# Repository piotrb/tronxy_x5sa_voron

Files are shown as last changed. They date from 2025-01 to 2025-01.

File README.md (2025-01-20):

# TronXY X5SA -> Voron Trident Conversion

Work in Progress

I opted for "topic" based mini readmes, so have a look in each folder and see what's there.

This should be mostly complete, ther's better ways to organize this all I'm sure, but this may get you somewhere closer to a full trident conversion.

Given this is fairly ... not step by step :) .. if you want to reach out to me I'm happy to help. 

You can find me as `.noobbait` on discord.

## Old Outdated Docs / V1 Conversion / etc

Ther's stuff in the [Archive](Archive) folder which is older .. especially the Old Docs folder there may have a bunch of additional detail that's not in these folders here.

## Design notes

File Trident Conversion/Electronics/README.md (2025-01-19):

This was a personal choice, but I really wanted the Inverted Electronics Bay option, and I also was a big fan of the EMS system.

So There is a few slight mods here for this particular purpose.

I also highly recommend swapping our the stock power supply for a genuine Meanwell PSU.

A Meanwell 350W PSU is thinner, so better airflow, and generally should just be safer :) .. Also, it only runs its Fan when it needs, to, rather than constanly .. 

I otherwise replaces all the other electronics, so you will need to make your own choices here.

You will also need to buy a proper power receptacle, the Tronxy one is odd sized and doesn't fit the "Adamtech" style, it felt a lot easier to just buy that rather than trying to make it fit.

BOM:

Item | qty | Notes
--- | --- | ---
Meanwell 350W PSU | 1 |
Power Recepticle | 1 |

## Chains

I tried to use the stock chains .. they're very crude .. 

I ended up just ordering some better ones from Aliexpress .. so the standard voron chain mounts work nicely.

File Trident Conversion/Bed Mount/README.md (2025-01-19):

Bed mounting was one of the more challenging parts of this conversion .. 

And a big reason why I gave up on the V1 conversion .. 

The "proper" voron bed setup is one of the most expensive parts of the printer, so I really wanted to be able to to avoid having to make that a requirement.

I ended up re-using some of the hardware that came with the bed .. those 10x10 square rods work really well to mount the very specific 6 screw mount .. 

Those 10x10 rods had to be cut down to size,

This is what this all looks like assembled:
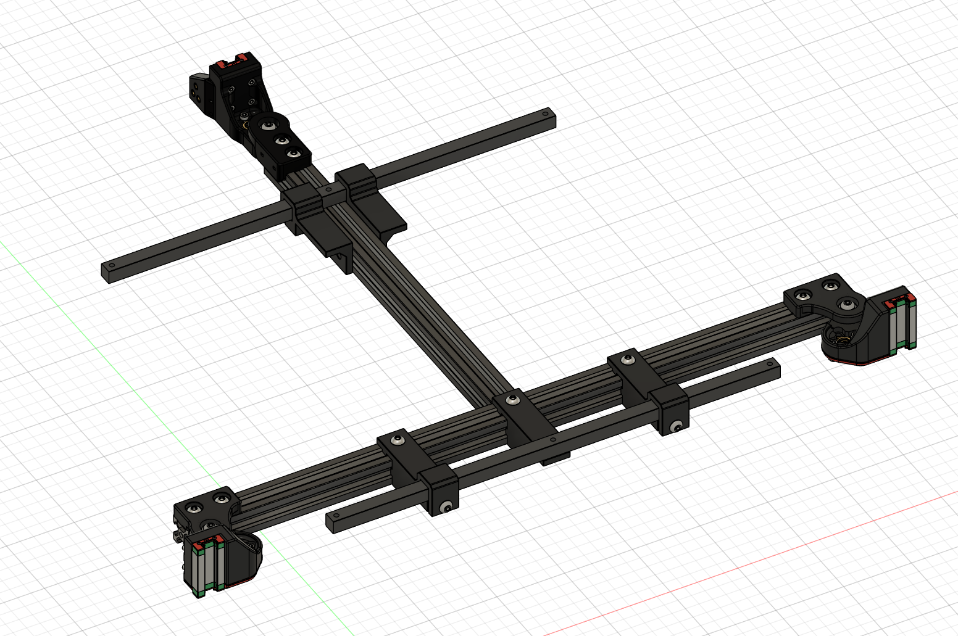
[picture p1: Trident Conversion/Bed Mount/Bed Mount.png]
Bed Mount


The pieces which fit around the 10x10 use a M5 25mm bolt, with a hex nut to secure it to the 10x10 rods.
With standard M5x10 bolts going into T-nuts or insert nuts to attach them to the extrusions.

I did away with the adjustment "wheels" and just used M3 nylock nuts to secure the bed screws.

I also swapped out the springs for these silicons spacers: https://www.aliexpress.com/item/1005003344878167.html
(it feels like it helped make things smoother)

Securing the back center bed screw is a bit finicky since it aligns with the 2020 extrusion.

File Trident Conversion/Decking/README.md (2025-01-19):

Nothing special here other than needing specifically sized decking.

BOM:

Item | Dimensions | Qty | Note
-|-|-|-
Corrugated Plastic | 473mm x 503mm | 1 | Back Panel
Corrugated Plastic | 458mm x 488mm | 1 | Decking
Corrugated Plastic | 478mm x 508mm | 1 | Bottom (optional)

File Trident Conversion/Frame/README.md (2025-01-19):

Ah frame .. 

You will need to buy some things here .. 

BOM:

Item | qty | Notes
--- | --- | ---
2020 Extrusion 420mm | 2 | (X axis) M5 tap on both ends
2020 Extrusion 360mm | 1 | (back horizontal) no tap
2020 Extrusion 405mm | 1 | (back vertical) M5 tap on one side only (both sides is ok, but only need one)

I had good success with this store: https://www.aliexpress.com/store/911747370 they have preset sized extrusions, but they will cut/tap them on request. They did that quite quickly for me and the packaging was great too, good padding, so there little change of damage in transit.

You can re-use the X extrusion from the Tronxy, but you will have to cut it down to size. It needs to be 450mm long.

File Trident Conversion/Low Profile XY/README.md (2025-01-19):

This is a special mod I made that fits around the 2040 extrusions the Tronxy uses.

The core pieces are the A/B Upper/Lower pieces.

This is a slightly less sturdy mount, but it doesn't waste any print volume.

I also gave the front idlers a similar treatment, but I did add some additional M3 holes so they can attach from a differnt direction, giving it all a pretty sturdy feel.

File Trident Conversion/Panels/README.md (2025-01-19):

## Panels:

You will want to get some 3mm acrylic panels

Exact dimensions coming .. 

Acrylic Transparent Panel 472mm x 502mm x 3mm | 1 | Top
Acrylic Transparent Panel 472mm x 544mm x 3mm | 2 | Sides
Acrylic Transparent Panel 472mm x 251mm x 3mm | 2 | Doors

Keep in mind that you likely will need to trim the panels for a final fit, so you will need a food file, or a dremel for this.

## Panel Clips

I wanted an easy way to remove my panels if needed .. I went through a few options here .. 

I ended up settling on these:

I had a bunch of spare M2 screws, so this seemed like a good option.
https://www.printables.com/model/643837-wide-voron-panel-snap-latch-with-lip-using-m2-scre

Ther's a M3 based option here, I didn't try it.
https://www.printables.com/model/702768-kit-for-removable-panelsdoors-for-voron-v2trident-

## Hinges:

I tried the clamping 270 degree hinges .. they kept slipping from the door .. so I switched to these:

https://github.com/VoronDesign/VoronUsers/tree/main/printer_mods/chrisrgonzales/270_degree_hinge

I also ended up needing to modify the way latches to work nicely .. see subfolders ..

I also use the latches from this, but I modified the "frame" side of the latch for a better fit/spacing. So feel free to use that or my mod, its not really specific to this conversion.

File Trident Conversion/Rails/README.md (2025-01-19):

Ther's a bunch of these .. and I definitely bought the wrong ones a few times :) 

BOM:

Item | qty | Notes
--- | --- | ---
350mm MGN9H | 2 | (for the Y)
450mm MGN12H | 1 | (for the X) -- this is wrong .. we need it to be 400mm I think

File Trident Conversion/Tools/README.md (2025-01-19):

## 105mm Y alignment spacer (print 2 of them)

this is used to align the Y axis when you're fastening the frame together.

Now I don't know if this was the best choice for sizing .. I feels a bit squisky in there .. 

I'm no longer sure why I opted for 105mm .. the Trident standard is actually 110mm .. so I don't necessarily recommend you follow my choice here ..

If I was doing this again I'd just do the voron standard here.

## the 115mm Extrusion Drill Guide

This is used to drill the access holes for attaching the Y axis crossbars

Many notes same as above .. it'd be 120mm per voron spec instead .. 

## Back Center Drill Guides

Print A and B (these should be printable diagonally on a 250mm print bed)

These just give you a nice way to drill the center access hole for the Back Z extrusion mount.

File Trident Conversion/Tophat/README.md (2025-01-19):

My particular choices necessitated a tophat .. (basically opting for umbilical .. which was always what I was going to do .. )

Needing custom sizing, and not really wanting to burn through rolls of ASA in prototyping this I decided for a very light weight tophat option.

I published this as a standalone mod:

https://www.printables.com/model/874142-minimal-tophat-using-4mm-coroplast-sides-flexible

If you need a tophat, you can give this a try. You can use the leftover coroplast from the decking/back/etc to use as side fillers.

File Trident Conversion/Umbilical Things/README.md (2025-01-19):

This folder is a bit of a catch all for a few odd mods I did to make everything work.

I ended up using this particular adapter for the back connector:

https://www.printables.com/model/326623-voron-trident-wire-cover-w-pg7-cable-gland-adapter

And the microswitch mount from here:

https://github.com/VoronDesign/VoronUsers/tree/main/printer_mods/Minsekt/Rear_Umbilical

This all worked out pretty well ...

I like these two because they together allow not needing a customized version of the AB motor mount system.

--

I don't have a lot of advice for the toolhead side of the umbilical .. 

I personally use the XOL toohead .. so the mounting is quite different, and I have my own mods here for that :) 

But there is plenty of PG7 cable gland adapters out there.

Just don't make the mistake I did and get the correct sized glands :)

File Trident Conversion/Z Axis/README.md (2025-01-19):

# Z Axis

## Z Mount Adapter

This piece allows you to use the stock Front Z motor mounts.

The Smaller version is for use with the inverted electronics mod mount variants.
The Regular is for the BOM variant.

You will need two of these, as well as:

* 4x M5x10 Socket Head Cap Screws
* 4x M5 Hex Nuts

## Z Motors .. 

I could have gone for the BOM lead screw motors .. but those tend to be expensive .. 

I did end up buying a set of "nicer" StepperOnline motors 

Also to have a matching set of motors to avoid any weirdness with having mismatched motors .. 

But you can totally do with the stock 2 Z motors, and then just add another ... similar one .. it *should* work, but YMMV :) 

The two Z screws that came with the Tronxy are the right length, you need another one of similar length for a full set for a trident.

I ended up going through a few options around the coupling of the motors and the lead screws .. in the end I ended up with these flexible couplings from Amazon that worked the best.

I would also recommend really carefully setting up your Z screw coupling, I had issues with the screw being a bit offset and rubbing on the leadscrew nut.

Speaking of which, I opted to get the POM leadscrew nuts, this worked out well for me, they seem to work well and are quiet.

Also, you know how the voron guide talks about keeping the leadscrew nut a but lose .. well you need that :) 

I also realized with some trial and error that you want to kind of offset the orientation of the screws that hold the nut .. 

- only 2 screws hold it, this is on purpose, this allows it some wiggle in the direction they're mounted.
- so assuming we use clock hand positions for the locations, you may want to set the back to 12 and 6, and the front (both of the front ones) to 3 and 9 .. this way the back can wiggle a bit forward and back, and the sides can wiggle a bit side to side. This should allow things to settle to a good position.

## Linear Rails

You will need 3x ~380mm linear rails (follow voron spec for the type and all, its just the length that changes)

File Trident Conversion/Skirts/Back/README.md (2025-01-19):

The back left and right pieces were fairly complex, they had the mounting for power/lan/usb/etc .. 

Also, it was the middle piece the stock build has of different sizes, so I just resized the center, use the side pieces from the stock build.

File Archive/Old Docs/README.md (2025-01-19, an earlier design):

This is a repo to track work I'm doing on converting a Tronxy x5sa to a Voron Chimera of some sort .. 

# High Level Objectives:

* Try to re-use as many parts as possible
* Try to make this into a gradual upgrade with "usable" milestones along the way.

# Milestones:

## 1. Open Frame V1.8 Style conversion

Goals:
* Mechanically everything works
* Printer *could* be enclosed at this point
* Some aspects could be rough and not quite pretty enough to request a serial
* At this phase, at least for me, I'll put on an Afterburner toolhead.
 * I have a few reasons:
   1. I have one leftover from my Switchwire when I upgraded it.
   2. I have some High Flow CHT heaters I've been itching to use, its easier to get volcano style mods for the AB .. they exist for the SB, but require an alternate whole Front piece .. which means I'd need to have two of those ready to go to be able to alternate between long and short nozzles ... 
   3. It just feels like a more modular design to hack on .. I've also been meaning to play with multi-material printing .. I even have a bunch of 2 in 2 out (and 2 in 1 out) heatsinks and whatnot .. my Switchwire was just annoying to try to build that onto :)
* Extra Credit: I've not seen a mod for this .. I'm going to try to see how I can either use the CW2 with the AB, or mod the CW1 so it mounts as easily as the CW2 (no back screws)

## 2. Enclosed V1.8 Style printer

Goals:
* Extra cost here, I will get Acrylic panels cut at this point
* I do plan to keep using coroplast for the opaque panels, its cheap and then I don't have to worry about the differences between the 1.8 and Trident Decking.
* This would qualify for a V1.8 Voron Serial
* Any final touches to make the electronics bay pretty and nicely cable routed.

## 3. Trident and beyond

* Start thinking about what would be needed to take this towards a trident design.
* I know the bed assembly will be a bit of a problem, so that will need some serious thought
* The rest actually shouldn't be too much of a problem, re-print a bunch of the parts, move the linear rails below the extrusions .. etc .. I'm already trying to hybridize Trident elements in the original design to make this as waste-less as possible.
* I'll likely wait until this phase to install the TAP, I have a kit for it kicking around, so I'm keen to know if the bed is now stable enough for it to be reliable.

In the "Beyond" category .. 

* Trident Idex?

# Build Notes:

[BOM](BOM.md)

[Frame and Skirt](Frame-and-Skirt.md)

[Z and Bed Assembly](Z-and-Bed-Assembly.md)

[XY Setup](XY-Setup.md)

---

# Credits & Acknowledgements

* [Sanity Agathion](https://forum.vorondesign.com/members/sanity-agathion.13/) on the VoronDesign Forum for encouraging me to go through with this build
* [@MatthewSitton](https://www.printables.com/@MatthewSitton_362947) on Printables for the amazing [TronXY X5SA CAD](https://www.printables.com/model/372048-tronxy-x5sa-full-cad-model) which made starting out on the Voron-izing work so much easier.

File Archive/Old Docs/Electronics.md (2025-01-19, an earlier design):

Alright .. so what do we do with the Electronics .. 

I had an Octopus Pro 1.0 kicking around so I plan to use that .. 
It also has CANBUS built in which is nice .. 

Its up to the reader to decide how you're going to wire this up .. 

Some basic info .. 

There is 4 core Drive Steppers:

Z1, Z2, X, Y

There is also the Extruder stepper if you're not using CANBUS .. if you are using CANBUS .. you can really even get away with using any basic controller board, and just wire up the Extruder stepper as Z2 .. 

---

Other bits .. 

The V1.8 design puts the steppers touching the left/right edges of the enclosure .. This blocks using oversized 60mm fans in the skirt area .. or at least for half of it .. 

I do kind of still want to try to use Noctua fans .. but their 60mm ones are 25mm thick .. 

I may see about instead of mounting them on one side and having them "blow through" .. I can set one up on the left, and one on the right .. and they can help eachother move air .. 

---

RPI setup .. 

I really wanted to improve on my old setup from when I did my Ender 3 conversion .. that had so little room underneath I opted to mount the RPI outside .. but here .. I can do it all inside .. 

The power hookup is a bit annoying with the main power switch on the intake .. I wanted some way to individually power cycle the MCU and the RPI .. 

For that you need the correctly power rated switches .. ideally small enough to be able to be mounted in the Hex holes in the skirts .. 

I found this model: https://www.printables.com/model/147203-voron-24-skirt-rocker-switch-skirt-fitting which gives a nice way to mount round switches in the Voron Skirt holes.

So here is the breakdown .. 

The 5V side is no real issue .. its so little power .. 

I had a RS25 PSU from the VORON BOM, so I used that .. 

Output: 5V 5A
Input: 0.7A/115VAC

This is a passively cooled PSU so I figured I can just put a switch on the DC line.

I found these guys on Amazon: https://www.amazon.ca/dp/B07W4HGMZS They seem to do the job well enough, and even though they say they're for 12V, the little status LED works just fine.

Now for the main board .. 

The stock PSU .. (I'll eventually want to replace it with a genuine meanwell .. but hey this project is about minimizing waste .. for now at least .. )
The stock PSU is a bit loud .. ther's writing on it implying that there is a thermal sensor toggling the FAN .. it feels like a lie .. with no load .. on a cold start .. it seems to still run the fan .. 

Ideally I'd love to be able to turn off that PSU entirely .. 

Now I could set the board to be able run its electronics off the USB power .. but that's not that useful .. since a CANBUS toolhead needs a 24V line to stay connected .. and Klipper will lose connection to the board if that disconnects .. 

So if that's the case the whole MCU may as well go offline .. 

anyways .. 

The one that came in my kit was:
Cheng Liang
Model: P360W24V

Input: 115/230VAC
Output: 24V 15A

Based on some random comment on an amazon review .. 

> Used 176 watts input for 144 watts output, about 81% efficiency.
> Uses 6.5 watts with no load.
> Power factor was 0.6, so doesn't seem there's power factor correction.
> The fan is decently loud. It's tied directly to the 24v output; it does not change speed based on load or heat as the description or case describes. With ambient noise measuring at 35db, meter shows 48db with fan on. -1 star for non-temperature controlled fan with higher noise than described.

If I understand this correctly .. 

81% efficiency means .. 
At max load of 360W .. it'd consume ~450W .. 
450W for 120VAC .. is about 4A

So I need a switch that's rated for at least 4A (double for safety .. so 8A)

I found this:

https://www.amazon.ca/gp/product/B09TXLNQVZ

Which claims its a 10A, with light .. I'm going to give this a try .. and it seems to be in the same form factor, which is great!

So long story short .. I'm going to have a way to toggle the actual AC power to the PSU

Now basically all switches I see on Amazon in this format seem to cap out at 24V 10A which is not enough for switching the whole output .. 
But maybe .. If I switch each component separately .. 

The Toolhead MCU won't need THAT much amps .. 
And the Octopus takes multiple power inputs .. separtaly for Motors, Bed, Logic/Fans .. this is great .. since that's pretty major power draw breakdowns .. 

Really hard to tell what the actual specs of the bed are in terms of power draw .. its all covered up with insulation and I don't want to rip it off .. and even that may not say anything .. 

My hotend probably uses something like a 50W cartridge .. plus a bit for the electronics/extruder .. so 2A .. Voron spec has the stepper running at 0.5A plus electronics .. so let's say 3A .. its nicely covered by the 10A rated switches .. 

Steppers .. 
Looks like Voron examples run then between 0.6A to 0.8A .. so even if we round that up to 1A .. that's 4A on the Motors line .. again totally fine .. 

Electronics .. Fans .. can't really be consuming that much power .. let's say that's 1A max .. 

so let's work this in reverse .. 

360W @ 24V = 15A
15 - ~3 (Toolhead) - ~4 (Motors) - ~1 (Electronics/Fans) = ~7A .. 

That would make the bed max ~165W .. or would it .. 

Looking around Aliexpress .. CR10 heated beds which are 310mm in size actually draw a LOT more power .. ~220W .. making them almost 10A .. 

SO even that should be ok .. except that the power supply wouldn't even have the juice for it ;)

...

Alright .. so if I do this .. 

BOM:

* 1x (or 2x if I decide to just match it up and add a switch for the 5V for parity) .. of those AC switches
* 1x of the lower rated 12V (5V works) switches for RPI power
* 3x of the higher rates 24V 10A switches for the various parts of the power system .. 

I don't know how this will work for routing all those wires around .. oh well .. worth a shot ..

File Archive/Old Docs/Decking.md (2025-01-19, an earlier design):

BOM:

Item | Dimensions | Qty | Note
-|-|-|-
Corrugated Plastic | 473mm x 503mm | 1 | Back Panel
Corrugated Plastic | 458mm x 488mm | 1 | Decking
Corrugated Plastic | 478mm x 508mm | 1 | Bottom

In the Voron 1.8 mode, I'm opting for a split deck design .. this allows for it to be easily removed from the top, even with the Z motors in place.

Given that the decking shape is quite different between the V1.8 and VT .. the decking will need to be replaced once in VT mode, not an issue with Corrugated Plastic being cheap :)

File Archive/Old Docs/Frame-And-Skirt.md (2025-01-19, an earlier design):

## Frame Extrusions:

Initially the frame is assembled as per the TrronXY instructions (ie the 12 main extrusions)

## Skirt Legs:

Because of the differences between using cleaner joints and just 2020 extrusions .. the M5 mounting hole on the Trident Legs ends up right over top one of the screws. So custom corner pieces have to be used. They're a minimal change to make the screw slot longer, this perhaps doesn't give it as firm of a hold, but it seems good enough.

I opted to just re-use the original rubber feet that came with the Tronxy, just stick a M5 screw through them and they work.

Materials Used:

Item | Qty | Notes
--- | --- | ---
M3x6 BHCS | 12 | for attaching the accent to the legs
M5x16 BHCS | 4 | for the actual rubber feet
M5 Nut | 4 | also for the rubber feet
The Tronxy rubber feet | 4 | you can easily put a M5 screw through them
M5 T-Nut | 4
M3 T-Nut | 4
M5x10 BHCS | 4 | or a couple of washers and a M5x12 .. its for the legs .. probably doesn't need to be that perfect
M3x8 SHCS | 4

## Skirt Panels:

Notes:

* Frame Depth is 10mm less than the 350mm spec .. which means I may have to use the 300mm spec side skirts .. and find a way to patch the gap .. 
* Width is 20mm more than the 350mm spec .. which means I will have to use the 350mm spec front/back center pieces, but stretch them by 20mm

I tried to re-use the original panels as much as possible. The only pieces I had to re-size was the center pieces, so the side pieces are original Trident parts. The side-middle and the front/back middles are slightly resized to cover the frame size differences.

## Electronics

I really like the idea of this mod: https://github.com/VoronDesign/VoronUsers/tree/master/printer_mods/LoganFraser/TridentInvertedElectronics

I hated having to flip my SwitchWire to access the elctronics .. this will need some tinkering .. 

It also mentions Using v2.4r2 Fan mounts .. I never really gave that a proper look .. it may make sense to consider skirt elements from the 2.4 instead ... 

## Front Display:

TODO. I'm not a huge fan of using the two ribbon mounted LCD's .. the wiring gets annoying and the functionality is so limited :) .. so I ended up just adapting one of the back blank pieces as a blank center piece. This conversion doesn't really do a display .. I may get around to resizing the display mount one day.

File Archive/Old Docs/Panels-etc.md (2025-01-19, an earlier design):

I tried the clamping 270 degree hinges .. they kept slipping from the door .. so I'm going to switch to these:

https://github.com/VoronDesign/VoronUsers/tree/main/printer_mods/chrisrgonzales/270_degree_hinge

Also considering this: 

https://github.com/VoronDesign/VoronUsers/tree/master/printer_mods/hernsl/bottom_panel_mag_clip

for the bottom panel

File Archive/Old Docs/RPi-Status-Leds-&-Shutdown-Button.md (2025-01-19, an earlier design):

So I wanted to have a front visible set of status LEDs and a power button to safely shut down the RPi without having to open the UI.

https://forums.raspberrypi.com/viewtopic.php?t=343731

https://github.com/raspberrypi/linux/blob/996f28d6295ad091f7edb462b52a91c8112019d1/arch/arm/boot/dts/bcm2711-rpi-4-b.dts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

https://github.com/raspberrypi/linux/blob/996f28d6295ad091f7edb462b52a91c8112019d1/Documentation/devicetree/bindings/leds/common.yaml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

https://forums.raspberrypi.com/viewtopic.php?t=101598

https://kitronik.co.uk/blogs/resources/which-resistor-should-i-use-with-my-led

https://kitronik.co.uk/blogs/resources/led-resistor-value-calculator

https://www.richinfante.com/2021/08/11/raspberry-pi-gpio-status-lights

--

I designed up a front "hex" mounted thing to hold the LEDs and the button .. 



I want to use 3 LEDs .. 

Green: System Status (so it should be "on" when the system is on)
Yellow: Disk Activity
Red: panic-indicator (fancy way to hopefully be able to see the RPi is crashed .. 

And I had a little button handy .. so it looks like this:
WhatsApp Image 2023-12-21 at 21 53 44_223efa18

Based on the docs available I should be able to just make that work with 3 dt-overlay lines .. 

```
dtoverlay=gpio-led,gpio=23,label=power,trigger=default-on,default-state=off
dtoverlay=gpio-led,gpio=25,label=panic,panic-indicator=true,default-state=off
dtoverlay=gpio-led,gpio=24,label=disk,trigger=disk-activity,default-state=off
```

---

Now I just have to get the wiring right .. 

- need to confirm that the status LEDs output 3.3v .. this is fairly sure thing .. 
- need to then figure out what resistor to use .. 
- based on the calculator .. 68 ohms should do it .. (Blue, Gray, Black)

Then something like this should work:

* note, I'm already using the first 6 pines in that row for controlling a PWM fan for the RPi itself, so this could clip in on the next 5 pins nicely



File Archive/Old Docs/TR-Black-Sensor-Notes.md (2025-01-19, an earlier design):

https://www.reddit.com/r/3Dprinting/comments/10971jk/my_progress_on_getting_the_tronxy_black_tr_sensor/

Its 6-24v in, the rest I will have to test with experiments .. seems like its switching on ground, so it'll need pull-up .. but otherwise should work .. 
With a 8mm effective range .. it may actually work nicely on a Volcano without having to re-adjust the probe position .. 

---

I ended up trying to make it work, but it seems like cloned omron sensors from Aliexpress do way better here .. I've since moved away from even that and use an Eddy probe.

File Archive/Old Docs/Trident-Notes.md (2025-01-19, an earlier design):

Bed Extrusions:

* 490mm
* 300mm

I may also want to copy the idea https://forum.vorondesign.com/members/dread.6231/ had around instead of modifying parts to fit the 2040's .. this can also be solved by just adding two 490mm extrusions at the front and back bottom at no loss of print volume .. I may do that .. this will add more extrusions to the conversion BOM .. but why not right? it'd be like maybe adding $20 to the BOM .. and allow using more stock parts .. 

so in that case .. 

* 2x 490mm

The extra extrusions should be M5 tapped .. 
The Bed extrusions .. I guess we only need the 300mm one to be tapped on one side

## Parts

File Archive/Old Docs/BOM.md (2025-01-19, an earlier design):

## The base printer kit

Item | qty | Notes
--- | --- | ---
Tronxy x5sa Kit | 1 | don't bother with the PRO, its just more leftovers

## Major Parts

Item | qty | Notes
--- | --- | ---
350mm MGN9H | 2 | (for the Y)
450mm MGN12H | 1 | (for the X) -- this is wrong .. we need it to be 400mm I think
DIN Rail 484mm | 2 |
Power Recepticle | 1 |
Piles of ASA filament | |
GT2 Open Belt LL-2GT-6 (6mm wide) | 6 meters |
F695 Bearing | 20 |
GT2 20T (6mm wide) Toothed Idler (5mm bore) | 2
GT2 20T (6mm wide) Pulley (5mm bore) | 2

## Toolhead

There will be no attempt at recycling the toolhead, there really doesn't seem much worth salvaging there. So the BOM will include basically the regular BOM for an AB or SB toolhead.

** I will try to re-use the TR Black bed sensor .. curious about it :) If that fails .. I do have a few spare Aliexpress voron spec Omron sensors.

## Small Parts

Item | qty | Notes
--- | --- | ---
M5x20-ish Bolts | 4 | for the legs
M5x16 BHSC Bolts | lots | these and the M6x10's are used for all sorts of mounting .. 
M5x10 BHSC Bolts | lots |
M3 T-Nuts | lots | skirts are held up by M3's mostly, and there will probably be more uses
* Most of the other bits so far there is plenty of spares in the Tronxy kit.

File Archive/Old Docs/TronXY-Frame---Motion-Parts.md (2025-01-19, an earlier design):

Frame:
* 2040 530mm x4
* 2020 530mm x4
* 2020 460mm x4

X Gantry:
* 2020 485mm x1

Z Motion:
* Linear Rod - 8mm - 527m long - x4
* Screw 8mm (M8?) - 450mm x 2

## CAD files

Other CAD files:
Trident Conversion/Skirts/Front/Center Front/Knomi V1/Main v2.stl
Trident Conversion/Bed Mount/Bed Front for 10x10 v4.stl
Trident Conversion/Low Profile XY/(Low Profile) A Wire Chain Anchor v3.stl
Trident Conversion/Panels/latch_x2 v3.stl
Trident Conversion/Skirts/Back/Center Back/Left v2.stl
Trident Conversion/Skirts/Corners/Corner (mirror) v3.stl
Trident Conversion/Skirts/Front/Center Front/Front Center Blank v2.stl
Trident Conversion/Skirts/Front/Center Front/Knomi V1/Retainer v2.stl
Trident Conversion/Skirts/Sides/Left Side v7.stl
Trident Conversion/Tools/115mm_extrusion_drill_guide v5.stl
Trident Conversion/Z Axis/Z Mount Adapter v2 (smaller) (option) x2.stl
V1 Conversion/STL/Frame/Back Center Drill Guide B.stl
Trident Conversion/Bed Mount/Bed Back Clip Mirror v4.stl
Trident Conversion/Low Profile XY/[a] (Low Profile) Y Endstop Bumper v3.stl
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

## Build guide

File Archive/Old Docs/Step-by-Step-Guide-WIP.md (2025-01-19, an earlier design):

# 1. Shopping

## 1. For the Frame

You will need to order a few extrusion pieces:
* 420mm (x2) with m5 tap on both ends
* 360mm (x1) no tap
* 405mm (x1) M5 tap on one side only (both sides is ok, but only need one)

I had good success with this store: https://www.aliexpress.com/store/911747370 they have preset sized extrusions, but they will cut/tap them on request. They did that quite quickly for me and the packaging was great too, good padding, so there little change of damage in transit.

While you're there also pick up:
* (at least 4pcs, they sold them in increments of 5) LM8LUU 8mm High quality Longer Linear Ball Bearing from them

The stock linear bearings can be damaged easily when trying to de-flange them .. so you may as well have spares, and they seemed smoother for me when I replaced them anyways.

# 2. Frame

Assemble the frame as per the Tronxy spec

Have a look over the blind joint information in the Trident Manual (Page 10)
https://github.com/VoronDesign/Voron-Trident/blob/main/Manual/Assembly_Manual_Trident.pdf

> [!IMPORTANT]
> Print out the drill guides for the blind joints as well as the spacing helpers. (you can print this in PLA if that makes it easier, these are disposable helpers)
> 
> You can find them in `STL/Frame` folder of the repo. These are specifically `105mm Y Alignment Spacer x2.stl`, `115mm Extrusion Drill Guide.stl` and `Back Center Drill Guide A.stl` (as well as the `Back Center Drill Guide B.stl` counterpart). You will need the last two in a second.

Drill out the ~4 mm access holes through the wide end of the 2040 extrusions as per the guide.

What this looks like:


> [!NOTE]
> TODO: add some photos/drawings on how to do this

Take off the top pieces of the frame, and slide in the pre-threaded cross-bars (420mm pieces) with M5x16 BHCS screws, and tighten them through the access holes. Use the spacing guides to help align the spacing to be as close a possible to even.

Between the Trident Assembly guide and the Trident Frame Upgrade guide you can find some tips visually on how this is supposed to come together. We're just using slightly different lengths of the drill guides.

https://github.com/VoronDesign/Voron-Trident/blob/main/Manual/Frame_Upgrade_Trident.pdf

> [!IMPORTANT]
> Also print out the bottom drill guides ..  (you can print this in PLA if that makes it easier, these are disposable helpers)

For the bottom access holes, I made a different kind of guide, made up of 2 parts, you slot it into the extrusion, and drill with a 3mm drill in the right spot which should be centered on the extrusion.

> [!NOTE]
> TODO: add some photos/drawings on how to do this

You will need to do a similar thing with the 405mm piece, just with a single screw, take apart as much of the frame as needed (probably just the two bottom screws holding the back bottom extrusion) and slide the vertical piece in. Tighten it using the access hole you made. This being exactly centered is not as big of a deal.

> [!IMPORTANT]
> Print out the back corner braces (ABS) (from the Trident STLs)
> 
> Located: https://github.com/VoronDesign/Voron-Trident/tree/main/STLs/Z_Assembly .. specifically `z_rear_extrusionbracket_left.stl` and `z_rear_extrusionbracket_right.stl`.

Secure them loosely to the frame (why not, take care of the loose piece of extrusion)

# 3. Skirts

Print a bunch of stuff (standard Voron settings)
1. Print the corner pieces as per Trident spec
2. Print the Fan holding assemblies as per Trident spec.
3. Print the 350mm spec Front left/right skirt pieces
4. Print the Rear Left/right pieces .. I did create a slight variant of the power inlet piece .. but it being a main "power" component (and generally cheap, I recommend you replace it with the Voron spec at least Adam tech version) .. but you can just use the stock one too .. up to you how you feel about the safety of the stock electrical components.
5. Print my customized extra large back center piece in 3 parts
6. Print my customized left/right skirt parts
7. Choice:
  a. Print the customized blank center piece
  b. Or print the stock Trident Mini12864 assembly
8. Choice:
  a. Print my customized stock foot adapters
  b. Or don't .. and purchase the stock larger round feet as per Trident spec, they're quite cheap and readily available on Amazon .. I liked this option more, it seems to allow the frame to feel more rigid on the feet.

Assemble all that basically according to the Trident spec, with the few customized pieces swapped in.'

You will likely need a bunch of fasteners here, a bunch of M3 SH screws, some M5 and a bunch of t-nuts, and I think an M5 Hex Nut for each foot.

# 4. Z Assembly

> [!IMPORTANT]
> Print out the Bed Mount trimming jig, and the Linear Rod trimming Jig.

1. Trim those parts as needed.
2. You will need to drill some M4 holes and Tap them (I think its ~3.5mm drill, but double check) .. the jig has the holes for where you need to drill.

> [!NOTE]
> TODO: add some photos/drawings on how to do this

Assemble the bed mount similar to how it would be for the Tronxy, but now using the trimmed mount positions.

1. Option:
  a. Try to de-flange the stock linear bearings -- you will likely need to cut the flange open on two ends and then try to pry it off. Be careful not to get filings into the inside of the bearings and not to lose balls from it due to the vibrations.
  b. Just buy some linear bearings (I suggested a store that also sells you the extra extrusion pieces) .. the bearings are quite cheap, so its a case of why not .. 
2. Print my custom linear bearing mounts
3. Print the Voron 1.8 Z motor mount plates and the linear rod fasteners
4. Choice:
  a. Try to trim the stock Z rods to the correct length ~350mm (I've not tried this)
  b. Or purchase some correctly sized rods (I had some leftovers from an Ender 3)
  c. Or purchase some motors with built in rods .. I've not done this .. I'm going to go with this option when I start converting towards a Trident design)
5. Assemble all of this together into a working Z mount (just the bed mount for now, don't attach the bed)

# 5. XY

1. You will need a bunch of components .. mostly pulleys, bearings, and fasteners.
2. You need to print my inverted versions of the XY system
3. I focused on making the "xy limit pod" system to work .. it possible to use the V1.8 style Y endstop located next to the motor .. and then we'd need a modified toolhead mount that allows for an endstop switch .. If there is enough interest I could try to design the right pieces to make that system work .. what I really gave up on trying to make work is the X chain setup .. the inverted components just don't fit a chain on the X properly .. so this setup expects to use an umbilical style setup, ideally with a CANBUS toolhead.
4. I bought some magnetic sensor pod board for the XY limit .. but you're free to use the standard microswitch version of it from the Voron Trident spec.
5. I have a fair bit of little modifications to attach the Y chain.

# 6. Bed

1. you will need the custom bits of mounting for the chain top and bottom .. 
2. and then you mount the bead .. with all its 6 leveling screws .. 
3. the chain attachment fits in-between the right back screws .. you want to fit that all before you mount the bed
4. I highly recommend getting the spring steel print surface for the Tronxy x5sa .. it seems overpriced .. but I think its worth it over the stock glass bed .. you can defainitly make do with the glass bed to start with

# 7. Toolhead

This setup can fit any regular Voron toolhead. Given we're not using any parts from the stock toolhead .. its your choice what setup you use here.

# 8. Electronics

1. Get a DIN rail .. ~1000mm will be just enough to cut the two pieces you need, with a tiny sliver leftover.
2. The stock PSU will work well enough with the Meanwell 350 mount pieces .. the only problem with it is that its a fair bit taller and basically there would be no air flow if you attach the bottom panel .. the stock PSU also does not turn off its FAN even when idle .. so its quite loud .. I'd recommend getting a genuine Meanwell 350 PSU, it's smaller and the fan turns off when not needed.
3. You will need a 4 driver controller board (so pretty much anything will do) .. 
4. A raspberry PI .. ideally a Pi4, a Pi3b will be ok if you don't run a camera

You will need to wire it all up in a way that makes sense :)

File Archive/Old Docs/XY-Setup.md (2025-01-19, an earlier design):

The XY will require a bunch of work .. 

First of all, there is a number of extrusions needed to be ordered .. 4 in total.

First there is the XY sub-level itself. This design is shared between the 1.8 and Trident.

On the Trident spec, this sub-level is ~105mm down from the top of the frame.

Item | Length | Qty | Instructions
--- | --- | --- | ---
Side Gantry Extrusions | 420mm | 2 | M5 Tap Both Ends
Back Motor Extrusion | 360mm | 1 | 

And then I also decided to use Trident's Back Support (and third Z rail) extrusion for extra support. This sets up the frame for being able to try to go Trident style 3 Z motors eventually.

Item | Length | Qty | Instructions
--- | --- | --- | ---
Back Support Extrusion | 405mm | 1 | M5 Tap One Side

## XY/AB assembly

Mechanically this should all work pretty similar to the 1.8/Trident setup .. but there is subtle differences between them and there will need to be more for this.

For one, the AB motor mounts will need to be altered to fit around a 2040 extrusion, this shouldn't be a big change in itself, so I'm not worried.

The placement of the limit switches will be a bit troublesome. I will probably need to custom design some variant of the X gantry attachment.

I'm going with the Trident style single linear rail design, but the Trident depends on mounting the X limit switch on the Frame end of the gantry (it uses a V2 style X/Y unified limit location). The 1.8 still has split limit switches .. anyways since I'm using the X mount from the Trident, I'll have to modify it to include the limit switch in the toolhead (so its back to 1.8/Switchwire style) .. probably anyways .. as I have the CAD closer to where it needs to be I'll see if there is any way I can re-use the v2/trident limit switch design .. but there may just not be room for it .. in those designs it depends on vertical linear rails, so it can put stuff below the rail Y extrusion .. in the linear rod design, those are in the way there .. so I'd have to find a way to literally flip that design and place all thar ABOVE the Y extrusion.

## Further Notes

The X extrusion will have to be cut down to ~450mm to make room for the Voron mounting on it.

The X linear rail I got will need to be cut to 400mm .. since there is more X distance being eaten up by the mount, I over-estimated what will be needed there.

I also played with the XY mounts .. and if I kind of rotate and swap them .. they end up seemingly aligning and fitting .. 

This also means that I would be able to use the fancy voron 2 style unified XY endstop board from the look of it

The chain path is a bit up in the air .. but it looks like it may work .. its a bit more .. specific now .. so I'm not sure that we can actually re-use the tronxy chains .. they are a bit clunky .. but the general idea seems to be that I'll be mounting the chains similar in principle as the standard 1.8 build does .. which is a chain fitting in the upper section above the Y axis .. the X chain should be no issue .. routing all the cables outside the chains may be a bit interesting too but I don't anticipate it being too much of a problem .. 

I ended up using Mirrors of ALL the XY drive mount pieces .. The X caps, the AB drives and the Y attachments .. this flips the belt path entirely, but it does so uniformly .. so we should be able to use the Trident style parts, but driven on TOP of the extrusion instead of below .. This all looks pretty good in CAD, waiting for my extrusions to arrive .. 

---

Belt lengths .. 

Without the "maximizing Y" mods .. the belts are ~190mm each .. 

with the maximizing mod .. we're adding .. just a bit under ~32mm length to the rail .. so 2x that of belt .. so ~64 .. so ~225 per side .. this is with a lot of padding ..

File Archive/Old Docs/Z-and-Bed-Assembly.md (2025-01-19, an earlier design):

The main problem I encountered with the Z / bed assembly is that it was designed to stick out the sides of the frame. If we're convering this into a proper enclosed Voron, we need to tuck all that inside.

There was few problems:

1. The Z motors were center mounted on the extrusion (so ~10mm overhang on each side)
2. The bed assembly itself was wider than the frame.
3. The linear rod bearings have giant flanges, making it impossible to use those if the linear rods were to be mounted on the frame.
4. The Bed mounting itself is a bit unique .. there is 3 holes very close to the edges of the bed on the front and back .. this doesn't really align very well with the Voron bed designs.

## Bed Assembly

The bed assembly is for the most part stock, the main difference is that the square rods had to be trimmed to fit inside the frame.
I played with a few ides but the main one I'm going to try to implement is a very Voron 1.8 style system.

1. Trim the square rods by `32mm` one each side (this will algin the original Screw/Rod plate with the new Z motor position
2. Drill & M3 Tap those rods to allow to use a similar to original 2 screw attachment to allow the bed frame to stay stable and square.

## Bed

For the most part stock ...

I may very quickly want to get a Spring Steel surface though .. not sure how much pain the stock Glass bed will be.

Note:

Looking at how this is fitting into CAD, a bunch of Y space is being eaten up at the back, so it'd be good to be able to create some alternate mount which shifts the bed a bit forward .. I will start trying to make this a light weight thing that can be just attached to the existing aluminum frame that comes with the Tronxy .. I wouldn't want to try to replace the whole mount until I'm working on switching to a more solid Trident 3 stepper setup .. 

## Note about Z Height

Due to the addition of the 1.8/Trident style Gantry level extrusions, the length of the Rods and Screws must be shortened.

See: [XY Setup](XY-Setup.md)

## Z Motors

The Motors will move inside the frame Voron 1.8 style (identical mounting part). They should align perfectly with the trimmed bed mount, so the original screw attachment can be re-used.

The motors do use a bit of a weird way of attaching to the metal plates, half of the stepper screws are longer and they were pulled through the plate.

* Short screw length: ~33.5mm with head .. 
* Long screw: 41.8 with head
* So ~8.3mm have to be trimmed down from those long ones
* And then 4x M3x12 screws can attach it to the V1.8 Z motor mounts
* In the early phases, I'm just using 2x M3x12, probably want to upgrade to 4 screws in the final fit

The Screw will have to be shortened. The how and by how much is TBD.

I have some old screws from my Ender 3 conversion, I may use that to test the cut/finish.

## Linear Rods

The rods will have to be shortened. The how and by how much is TBD.

They will be mounted similar to the 1.8 style with those little accent mount pieces.

They will also align perfectly with the original holes at the bottom at least, so they can actually get a but of extra alignment help and support from the bottom there.
At the top they will just be held by the printed holder (this is good, since it will allow for easy final alignment.

The attachment to the bed frame will be interesting.

Ideally I'd like to re-use the original bearings, after all the goal of this project is to waste as little as possible :). In order to do that I'll have to remove the flanges from those bearings, and then press-fit them into redesigned part that's based on the 1.8 mount. Now I don't actually understand how the 1.8 part was normally fitted, or how tight it was, etc .. from some trial fits, it feels very snug when I try to insert the bearing into it .. but maybe that's good .. it'll hold in place well :) .. hope the ASA I printed the part from is strong enough to take a bit of stretch.

Worst case 4 `LM8LUU` bearings will need to be added to the BOM. I will try to cut the flanges off though first and see if I can salvage them, they appear to be heat fitted (but I don't want to heat it up with the bearing inside, since that feels like it'll melt/damage it), so I'll just have to try to cut it.

Update 1:

The rods will need to be shortened by ~123mm. I designed a cutting jig to make it easier to get the size right.
Still need to see how well my dremel rotary tool will handle cutting the rods.

Trying to figure out how long the screws should be .. this calculation is a bit tricky .. 

In the Voron 1.8 design .. the screws are well below the top of the linear rods .. 
But the trick seems to be to basically algin it so that the linear bearing assemblies touch the top printed stopper .. everything above that is extra rod .. 

I probably want to finish the CAD a bit more before I make that final determination .. since I have a bit of catching up to do in order to reflect the final state of the bed/Z in the current design .. then I can figure out how much the rods need to be cut .. not like that will be an issue until I'm ready to actyally put in the X axis anyways .. 

Ok on a quick look .. ~95mm may need to be chopped off .. I just need to figure out how to finish that cut ... its one of the few things that may need a half decent finish .. 

Also if the original screw is ~453mm .. chopping 95mm would put it at about 358mm total .. my old ender Z screws may actually work here .. they're just around this size .. so I'll have to play with it .. it  at least gives me a backup plan .. and a better sized "make do" option .. 

Yup my old screws are perfect length, so I didn't need to figure out how to cut them .. not using the voron spec stepper with embedded screw type things some Z height will be lost at the bottom ..

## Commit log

2023-12-19 Add Frame Tools
    [105mm Y Alignment Spacer x2.stl, 115mm Extrusion Drill Guide.stl, Back Center Drill Guide A.stl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]
2024-03-20 add a batch of STLs
    [105mm Y Alignment Spacer x2.stl, 115mm Extrusion Drill Guide.stl, A_Drive_Frame_Lower v8.stl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]
2024-03-29 Updated low profile parts
    [A_Drive_Frame_Lower v8.stl, A_Drive_Frame_Lower.stl, A_Drive_Frame_Upper v8.stl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]
2024-04-02 updated models
    [(Low Profile) A Wire Chain Anchor v3.stl, [a] (Low Profile) Y Endstop Bumper v3.stl, [a] Y_Endstop_Bumper.stl]
2025-01-19 First main more or less complete push
    [105mm Y Alignment Spacer x2.stl, 105mm_Y_alignment_spacer_x2 v8.stl, 115mm Extrusion Drill Guide.stl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]
2025-01-23 add V1 CAD
    [Tronxy Voron (V1) v69.f3z]
